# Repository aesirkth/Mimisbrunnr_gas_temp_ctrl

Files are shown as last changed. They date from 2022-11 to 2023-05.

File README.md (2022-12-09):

# Mimisbrunnr_gas_temp_ctrl

Mímisbrunnr gas tank temperature control unit

Project hierarchy: Mjölnir → Mimisbrunnr

## About

Mímisbrunnur is a temperature control unit that controls the temperature of the N<sub>2</sub> gas tank that is used as the oxidizer for the Mjölnir rocket.
The unit will regulate the temperature the desired temperature.
It will measure the temperature of the tank and then turn on a pump to allow warm water to flow in a tube around the tank.

## Requirements
1. Regulate the temperature of the oxidizer gas tank for the Mjölnir rocket
2. Manual as well as digital controls
    1. Manual control:
        1. Screen to see configurations
        2. Buttons to control
    2. Digital control:
        1. Connect through wifi and integrated into the system of Mjölnir
        2. Option to connect through CAN bus
3. Measure the temperature
    1. Have 3 temperature sensors: 1 top, 1 middle, 1 bottom
4. Turn a water pump to heat the tank
5. Tolerate rainy, snowy or other similar weather conditions

### Optional Requirements
1. Control heating element
2. Fully Waterproof

## Usage

Buttons to navigate

Connectors

## PCB

## Box

## Software

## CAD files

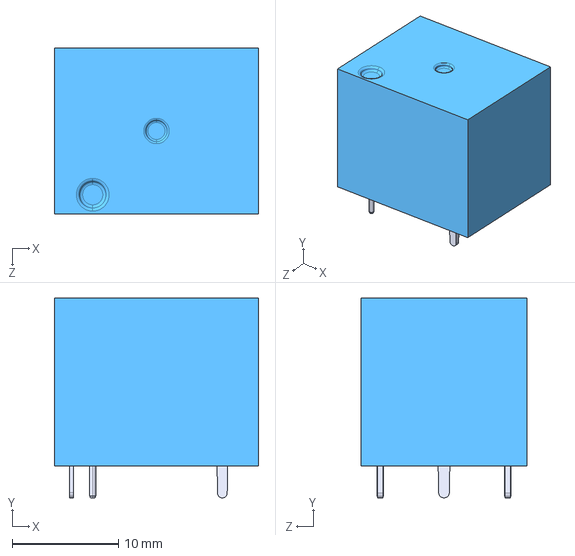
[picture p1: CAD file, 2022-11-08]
Mimisbrunnr_PCB/external components/SRD-12VDC-SL-C/SRD-12VDC-SL-C.step
19.2 x 18.8 x 15.6 mm

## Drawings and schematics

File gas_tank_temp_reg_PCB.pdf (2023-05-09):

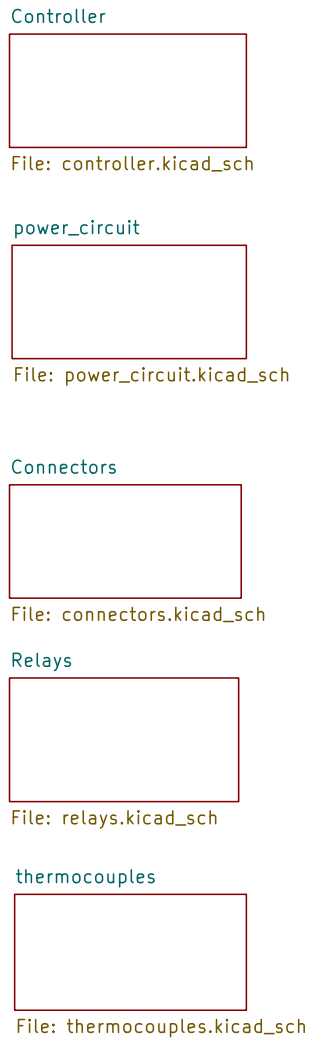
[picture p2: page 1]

Relays File: relays.kicad_sch Controller File: controller.kicad_sch Connectors File: connectors.kicad_sch

Id: 1/6 Title: File: gas_tank_temp_reg_PCB.kicad_sch Sheet: /

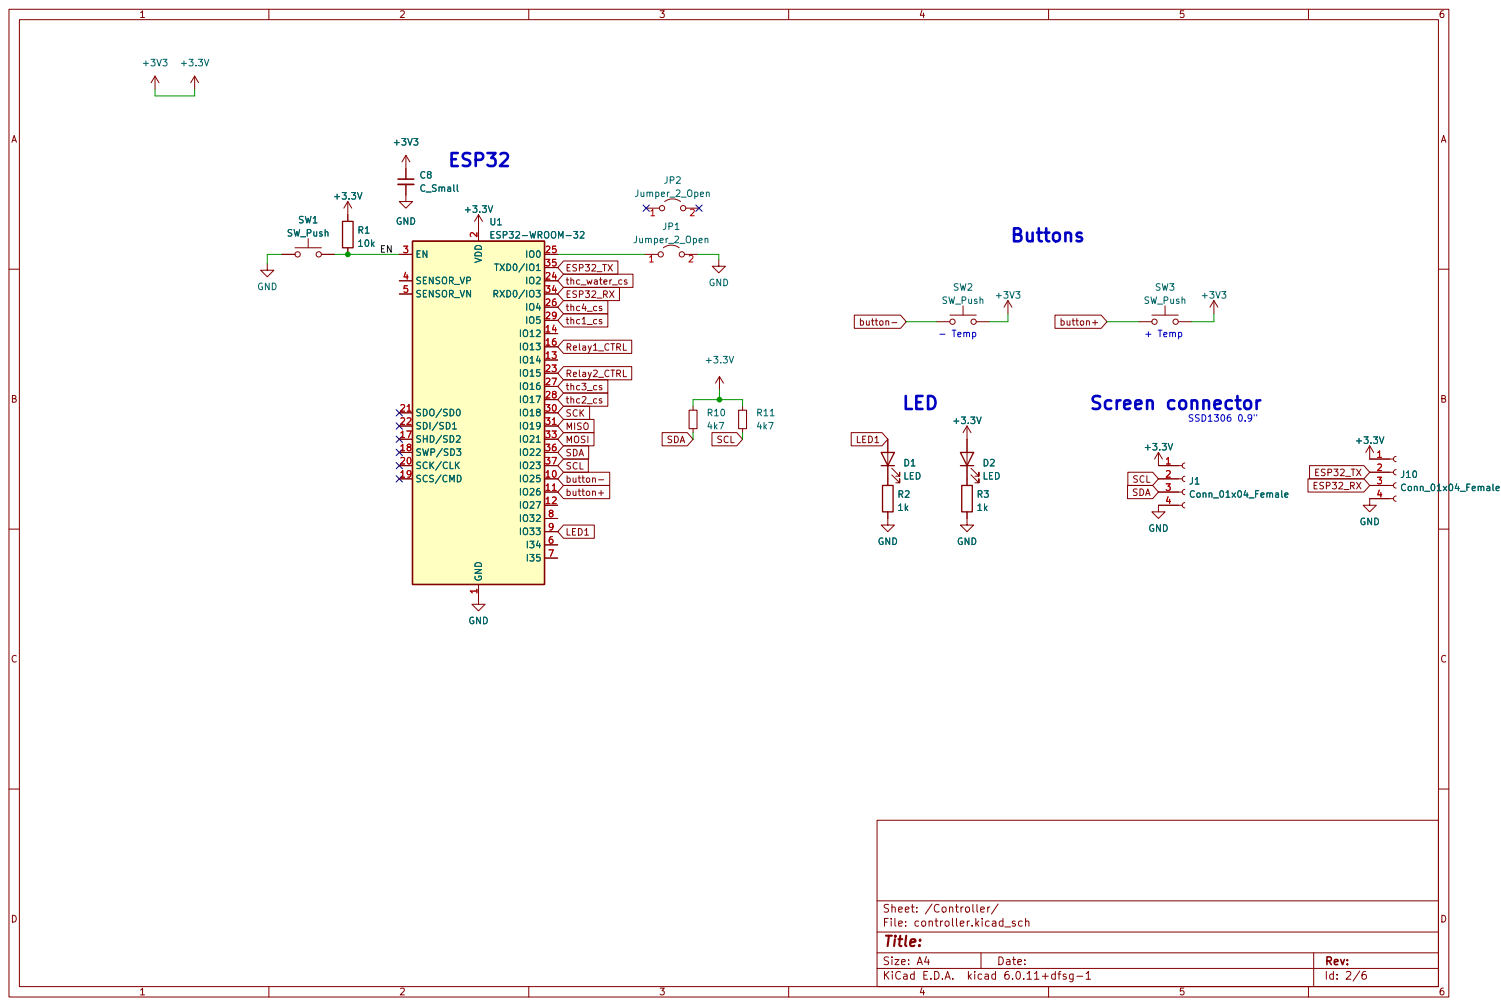
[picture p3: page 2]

2 SCK/CLK 20 SDO/SD0 21 SDI/SD1 22

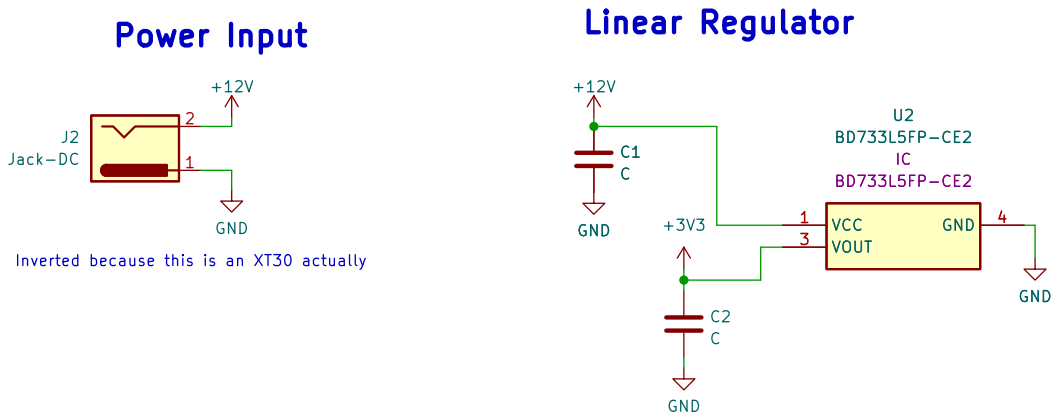
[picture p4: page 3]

Inverted because this is an XT30 actually

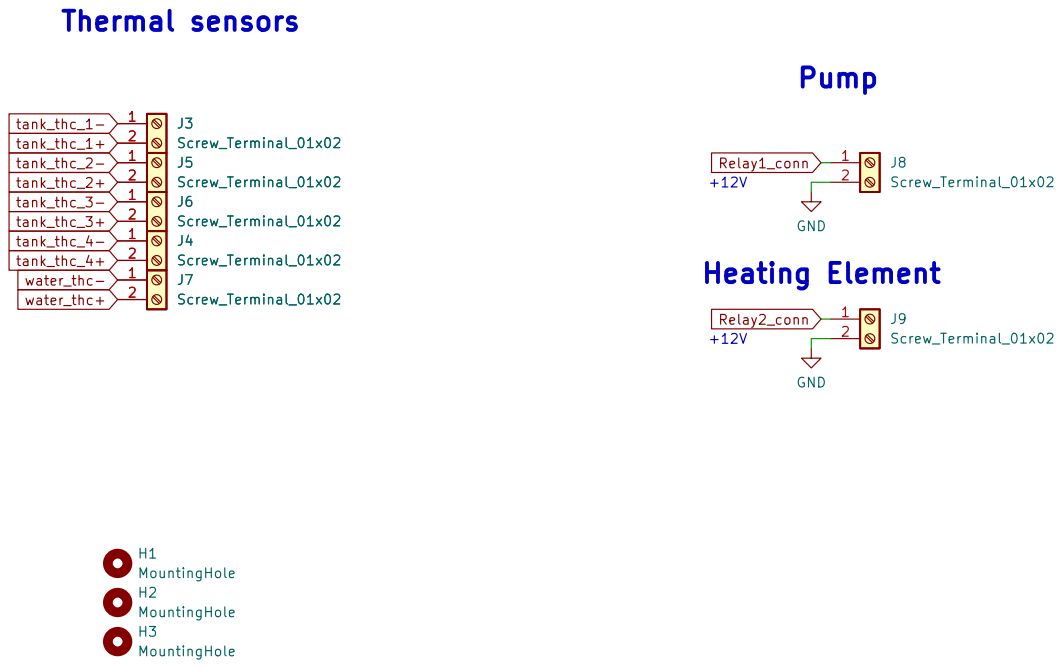
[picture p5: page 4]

Id: 4/6 Title: File: connectors.kicad_sch Sheet: /Connectors/ GND
+12V Heating Element

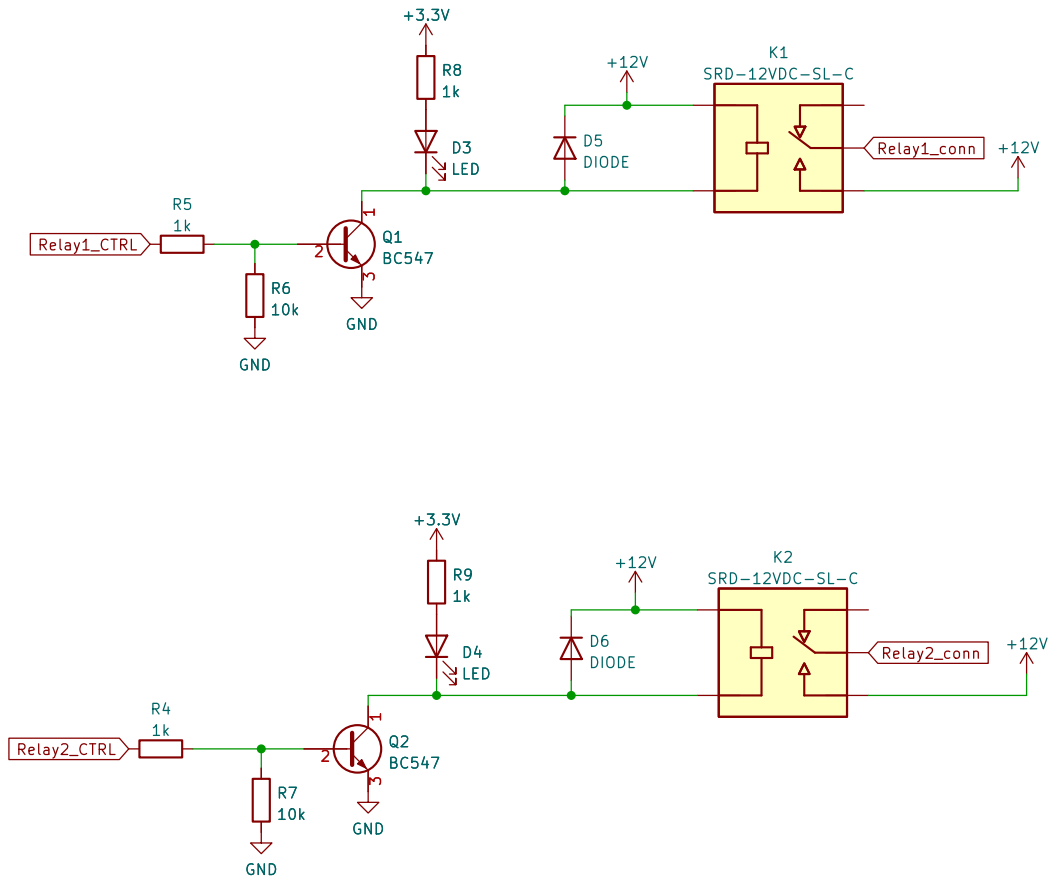
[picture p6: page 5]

Id: 5/6 Title: File: relays.kicad_sch Sheet: /Relays/

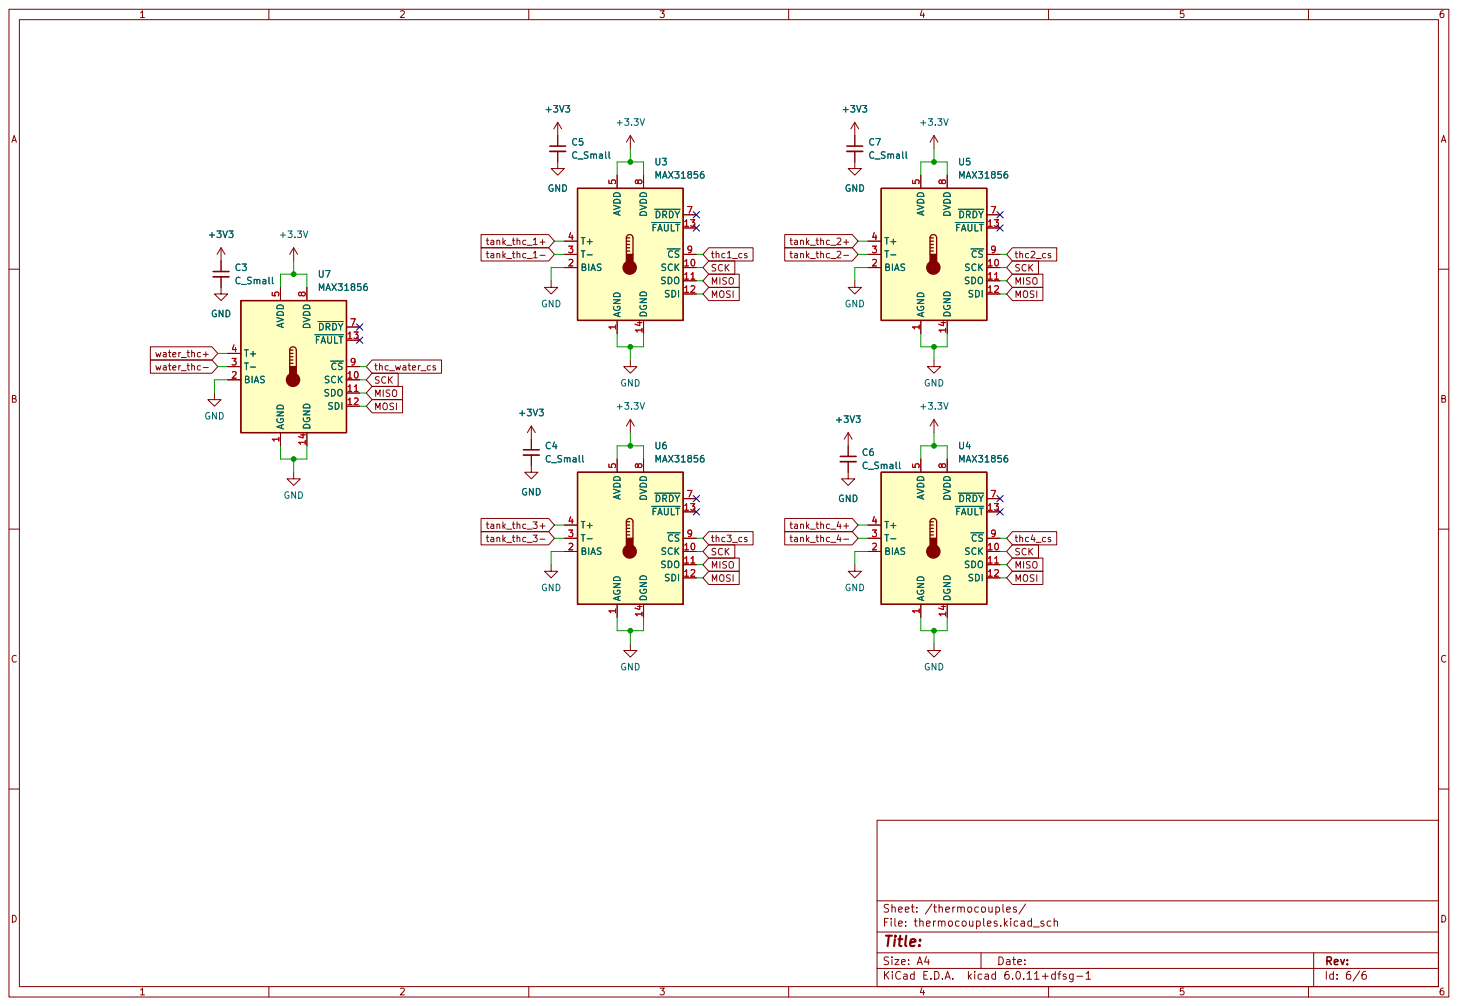
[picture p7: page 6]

1 SCK 10 SDO 11 SDI 12 ~{FAULT} 13 DGND 14 BIAS 2 T- 3 T+

8 ~{CS}9 U6 MAX31856 GND GND MISO

Id: 6/6 Title: File: thermocouples.kicad_sch Sheet: /thermocouples/

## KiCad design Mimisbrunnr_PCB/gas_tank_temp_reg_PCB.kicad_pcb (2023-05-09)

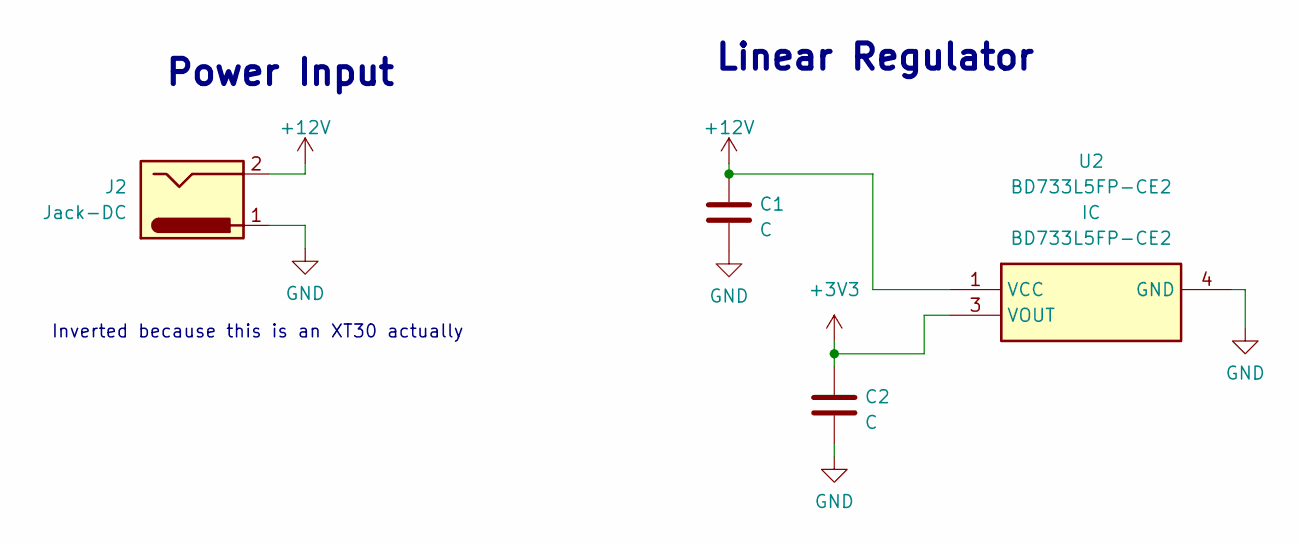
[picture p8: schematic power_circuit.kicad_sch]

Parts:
C1, C2: C; C_0805_2012Metric
J2: Jack-DC; AMASS_XT30PW-M_1x02_P2.50mm_Horizontal
U2: BD733L5FP-CE2; BD750L5FPCE2; Mouser Part Number 755-BD733L5FP-CE2

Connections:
+3.3V: C2.1, U2.3 (VOUT); also elsewhere on the board
+12V: C1.1, J2.2, U2.1 (VCC); also elsewhere on the board
GND: C1.2, C2.2, J2.1, U2.4 (GND); also elsewhere on the board

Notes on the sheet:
Power Input
Linear Regulator
Inverted because this is an XT30 actually

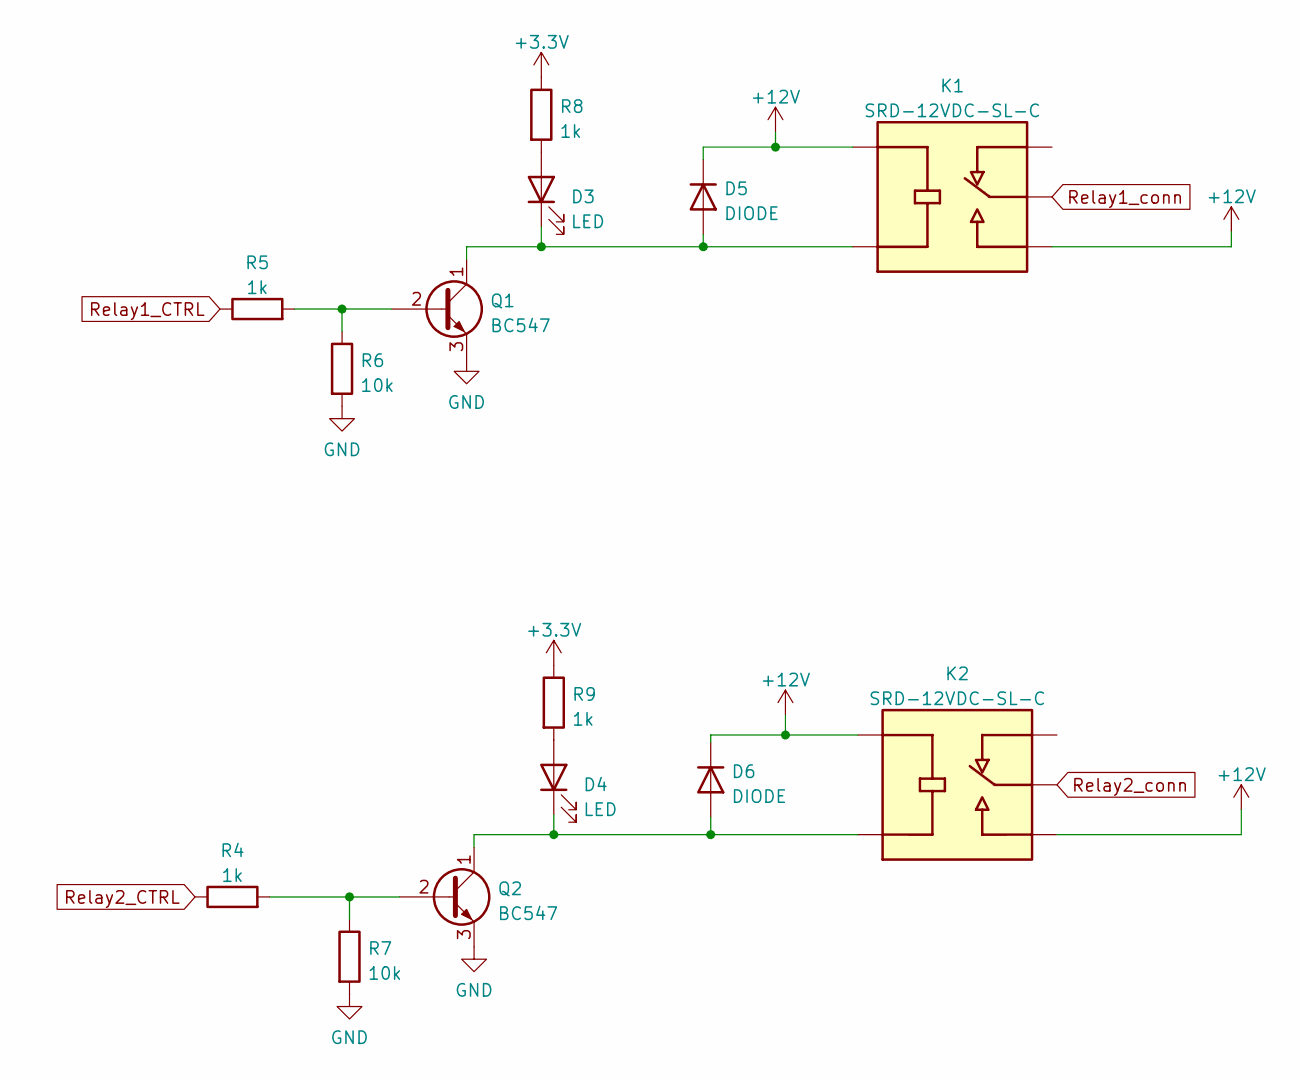
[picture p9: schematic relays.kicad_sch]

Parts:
D3, D4: LED; LED_0805_2012Metric
D5, D6: DIODE; D_0805_2012Metric
K1, K2: SRD-12VDC-SL-C; RELAY_SRD-12VDC-SL-C; PARTREV 1.0
Q1, Q2: BC547; TO-92_Inline
R4, R5, R8, R9: 1k; R_0805_2012Metric
R6, R7: 10k; R_0805_2012Metric

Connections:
+3.3V: R8.1, R9.1; also elsewhere on the board
+12V: D5.2 (K), D6.2 (K), K1.COIL1, K1.NO, K2.COIL1, K2.NO; also elsewhere on the board
GND: Q1.3 (E), Q2.3 (E), R6.2, R7.2; also elsewhere on the board
unnamed: D3.1 (K), D5.1 (A), K1.COIL2, Q1.1 (C)
unnamed: D3.2 (A), R8.2
unnamed: D4.1 (K), D6.1 (A), K2.COIL2, Q2.1 (C)
unnamed: D4.2 (A), R9.2
unnamed: Q1.2 (B), R5.2, R6.1
unnamed: Q2.2 (B), R4.2, R7.1
Relay1_CTRL: R5.1; also elsewhere on the board
Relay1_conn: K1.COM; also elsewhere on the board
Relay2_CTRL: R4.1; also elsewhere on the board
Relay2_conn: K2.COM; also elsewhere on the board

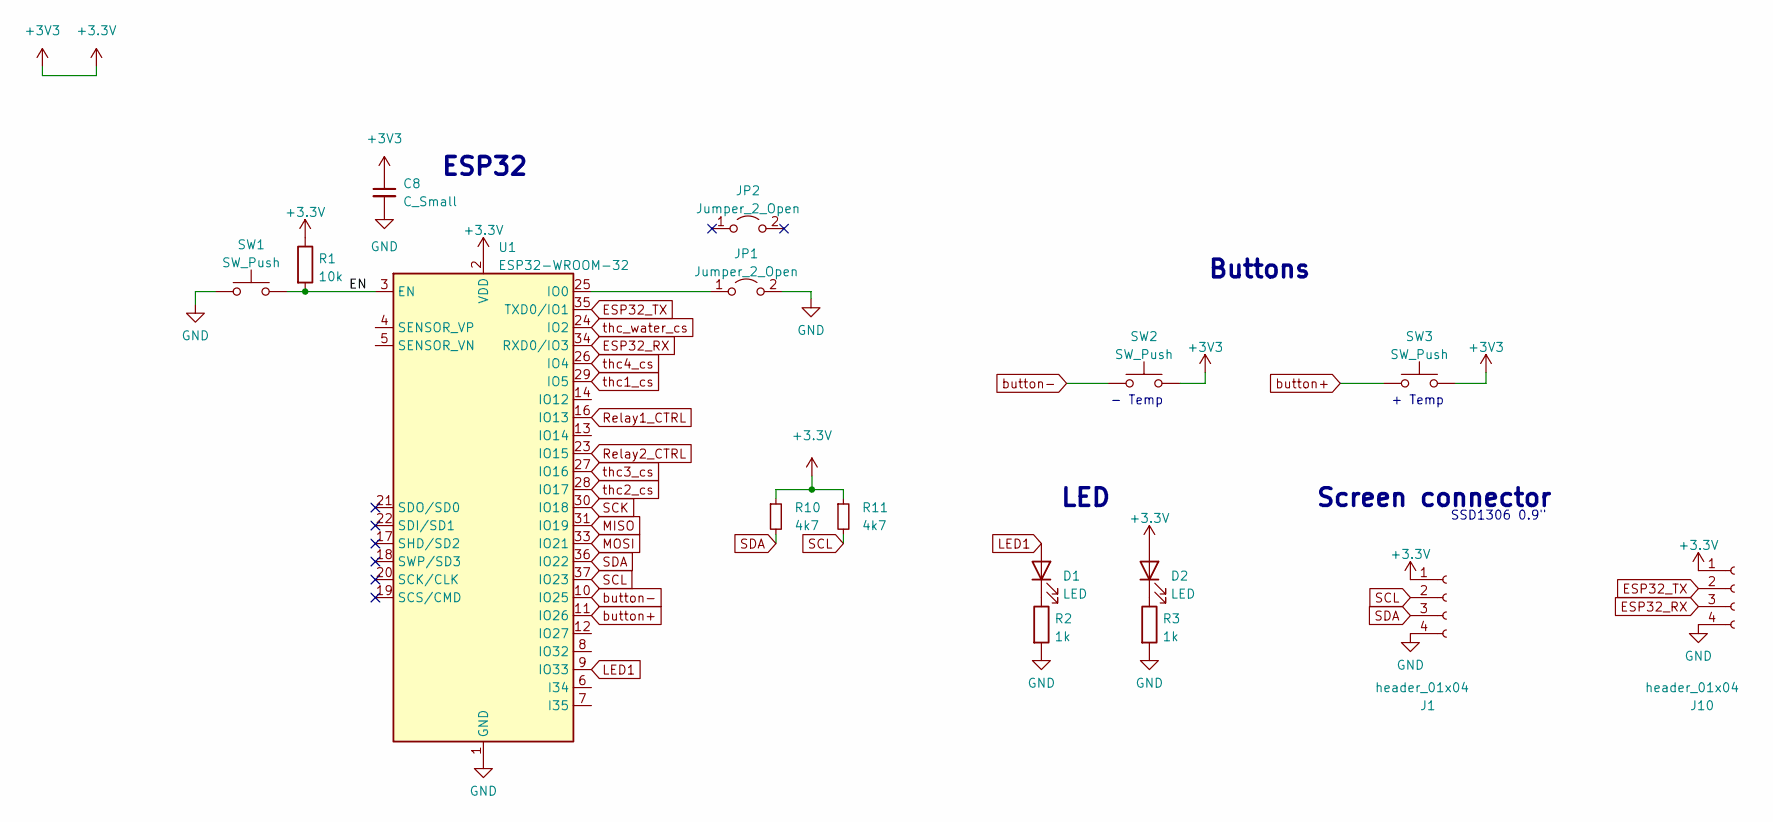
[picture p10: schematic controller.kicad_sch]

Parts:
C8: C_Small; C_0805_2012Metric
D1, D2: LED; LED_0805_2012Metric
J1, J10: header_01x04; PinHeader_1x04_P2.54mm_Vertical
JP1, JP2: Jumper_2_Open; PinHeader_1x02_P2.54mm_Vertical
R1: 10k; R_0805_2012Metric
R2, R3: 1k; R_0805_2012Metric
R10, R11: 4k7; R_0805_2012Metric
SW1, SW2, SW3: SW_Push; SW_SPST_B3U-1000P
U1: ESP32-WROOM-32

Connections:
+3.3V: C8.1, D2.2 (A), J1.1, J10.1, R1.1, R10.1, R11.1, SW2.2, SW3.2, U1.2 (VDD); also elsewhere on the board
/Controller/EN: R1.2, SW1.2, U1.3 (EN)
ESP32_RX: J10.3, U1.34 (RXD0/IO3)
ESP32_TX: J10.2, U1.35 (TXD0/IO1)
GND: C8.2, J1.4, J10.4, JP1.2 (B), R2.2, R3.2, SW1.1, U1.1 (GND), U1.15 (GND), U1.38 (GND), U1.39 (GND); also elsewhere on the board
LED1: D1.2 (A), U1.9 (IO33)
MISO: U1.31 (IO19); also elsewhere on the board
MOSI: U1.33 (IO21); also elsewhere on the board
unnamed: D1.1 (K), R2.1
unnamed: D2.1 (K), R3.1
unnamed: JP1.1 (A), U1.25 (IO0)
Relay1_CTRL: U1.16 (IO13); also elsewhere on the board
Relay2_CTRL: U1.23 (IO15); also elsewhere on the board
SCK: U1.30 (IO18); also elsewhere on the board
SCL: J1.2, R11.2, U1.37 (IO23)
SDA: J1.3, R10.2, U1.36 (IO22)
button+: SW3.1, U1.11 (IO26)
button-: SW2.1, U1.10 (IO25)
thc1_cs: U1.29 (IO5); also elsewhere on the board
thc2_cs: U1.28 (IO17); also elsewhere on the board
thc3_cs: U1.27 (IO16); also elsewhere on the board
thc4_cs: U1.26 (IO4); also elsewhere on the board
thc_water_cs: U1.24 (IO2); also elsewhere on the board

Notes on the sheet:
Buttons
Screen connector
+ Temp
ESP32
- Temp
LED
SSD1306 0.9"

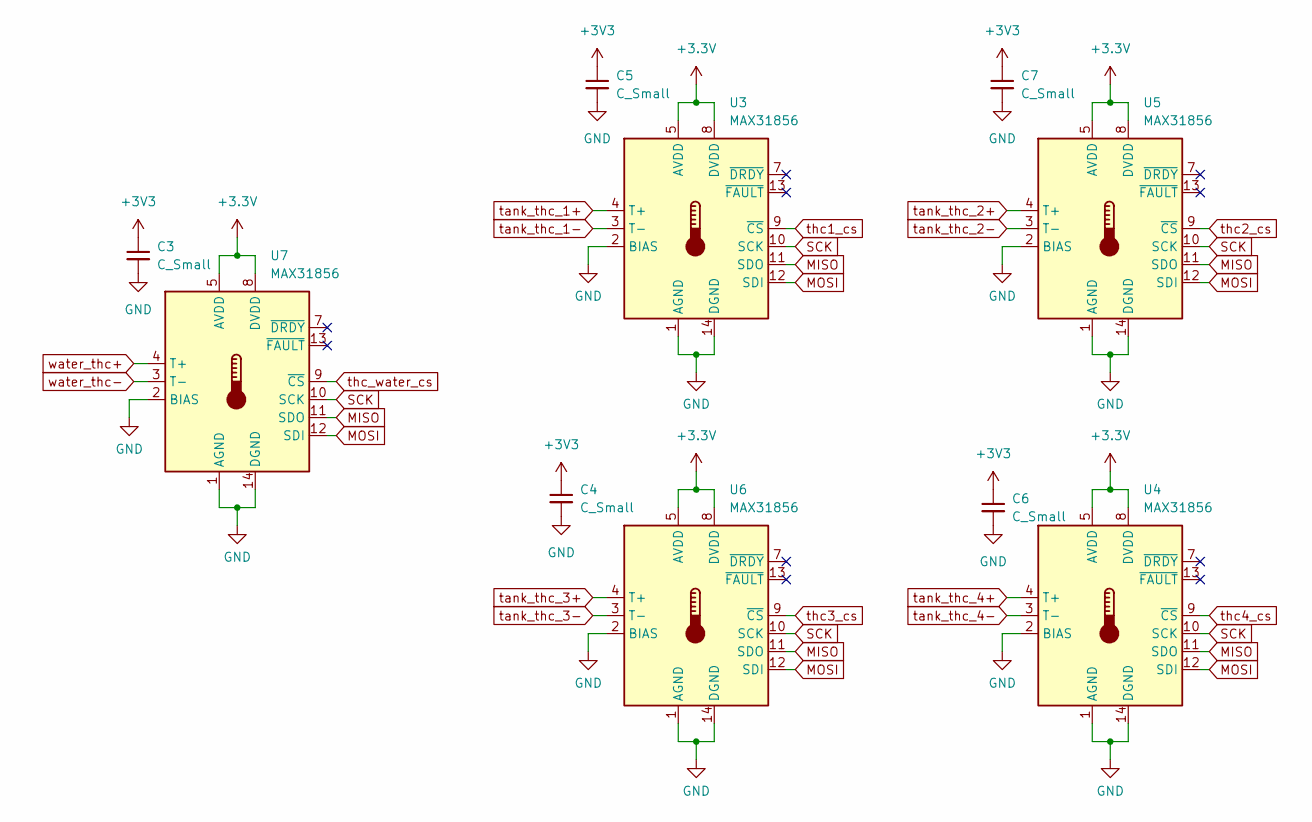
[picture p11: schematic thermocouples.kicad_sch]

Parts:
C3, C4, C5, C6, C7: C_Small; C_0805_2012Metric
U3, U4, U5, U6, U7: MAX31856; TSSOP-14_4.4x5mm_P0.65mm

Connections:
+3.3V: C3.1, C4.1, C5.1, C6.1, C7.1, U3.5 (AVDD), U3.8 (DVDD), U4.5 (AVDD), U4.8 (DVDD), U5.5 (AVDD), U5.8 (DVDD), U6.5 (AVDD), U6.8 (DVDD), U7.5 (AVDD), U7.8 (DVDD); also elsewhere on the board
GND: C3.2, C4.2, C5.2, C6.2, C7.2, U3.1 (AGND), U3.2 (BIAS), U3.14 (DGND), U4.1 (AGND), U4.2 (BIAS), U4.14 (DGND), U5.1 (AGND), U5.2 (BIAS), U5.14 (DGND), U6.1 (AGND), U6.2 (BIAS), U6.14 (DGND), U7.1 (AGND), U7.2 (BIAS), U7.14 (DGND); also elsewhere on the board
MISO: U3.11 (SDO), U4.11 (SDO), U5.11 (SDO), U6.11 (SDO), U7.11 (SDO); also elsewhere on the board
MOSI: U3.12 (SDI), U4.12 (SDI), U5.12 (SDI), U6.12 (SDI), U7.12 (SDI); also elsewhere on the board
SCK: U3.10 (SCK), U4.10 (SCK), U5.10 (SCK), U6.10 (SCK), U7.10 (SCK); also elsewhere on the board
tank_thc_1+: U3.4 (T+); also elsewhere on the board
tank_thc_1-: U3.3 (T-); also elsewhere on the board
tank_thc_2+: U5.4 (T+); also elsewhere on the board
tank_thc_2-: U5.3 (T-); also elsewhere on the board
tank_thc_3+: U6.4 (T+); also elsewhere on the board
tank_thc_3-: U6.3 (T-); also elsewhere on the board
tank_thc_4+: U4.4 (T+); also elsewhere on the board
tank_thc_4-: U4.3 (T-); also elsewhere on the board
thc1_cs: U3.9 (~CS); also elsewhere on the board
thc2_cs: U5.9 (~CS); also elsewhere on the board
thc3_cs: U6.9 (~CS); also elsewhere on the board
thc4_cs: U4.9 (~CS); also elsewhere on the board
thc_water_cs: U7.9 (~CS); also elsewhere on the board
water_thc+: U7.4 (T+); also elsewhere on the board
water_thc-: U7.3 (T-); also elsewhere on the board

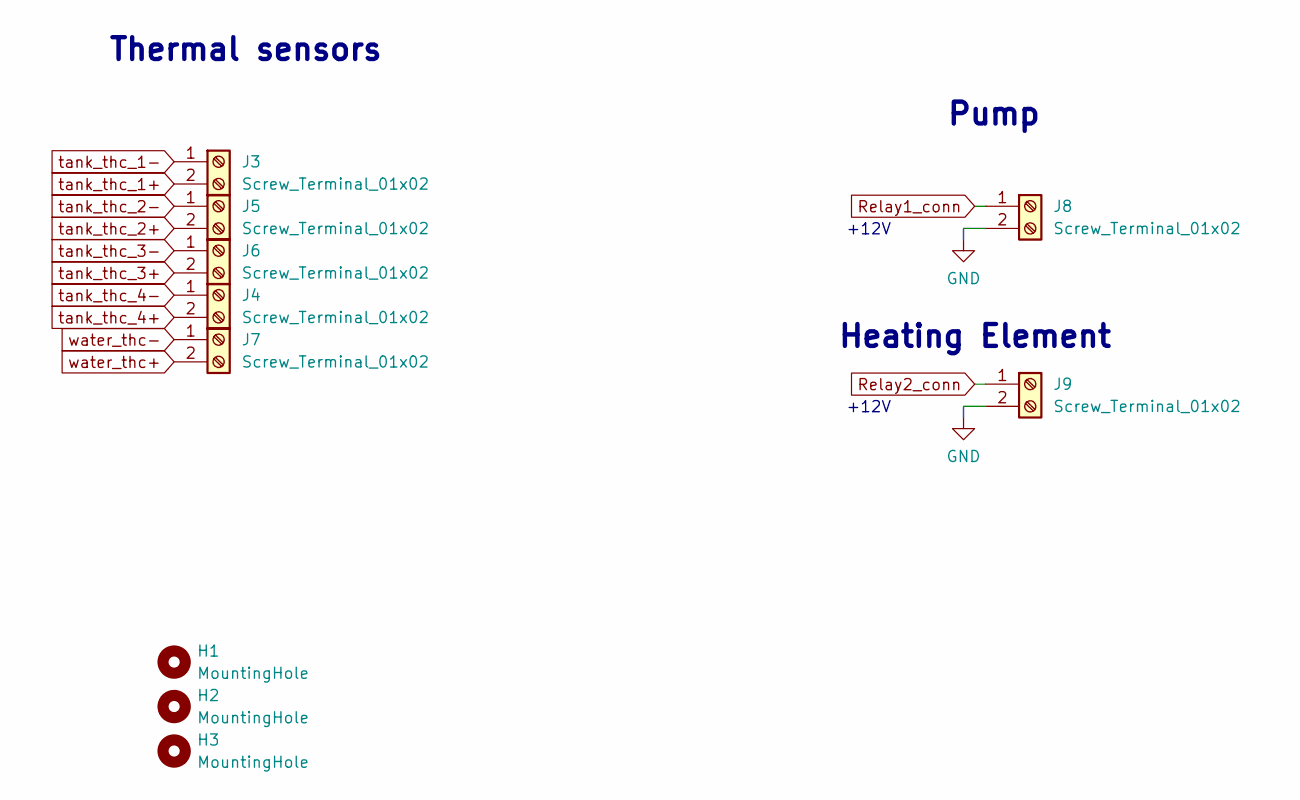
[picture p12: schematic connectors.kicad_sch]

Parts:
H1, H2, H3: MountingHole; MountingHole_3.2mm_M3
J3, J4, J5, J6, J7, J8, J9: Screw_Terminal_01x02; TerminalBlock_TE_282834-2_1x02_P2.54mm_Horizontal

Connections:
GND: J8.2, J9.2; also elsewhere on the board
Relay1_conn: J8.1; also elsewhere on the board
Relay2_conn: J9.1; also elsewhere on the board
tank_thc_1+: J3.2; also elsewhere on the board
tank_thc_1-: J3.1; also elsewhere on the board
tank_thc_2+: J5.2; also elsewhere on the board
tank_thc_2-: J5.1; also elsewhere on the board
tank_thc_3+: J6.2; also elsewhere on the board
tank_thc_3-: J6.1; also elsewhere on the board
tank_thc_4+: J4.2; also elsewhere on the board
tank_thc_4-: J4.1; also elsewhere on the board
water_thc+: J7.2; also elsewhere on the board
water_thc-: J7.1; also elsewhere on the board

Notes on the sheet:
Heating Element
+12V
Pump
Thermal sensors

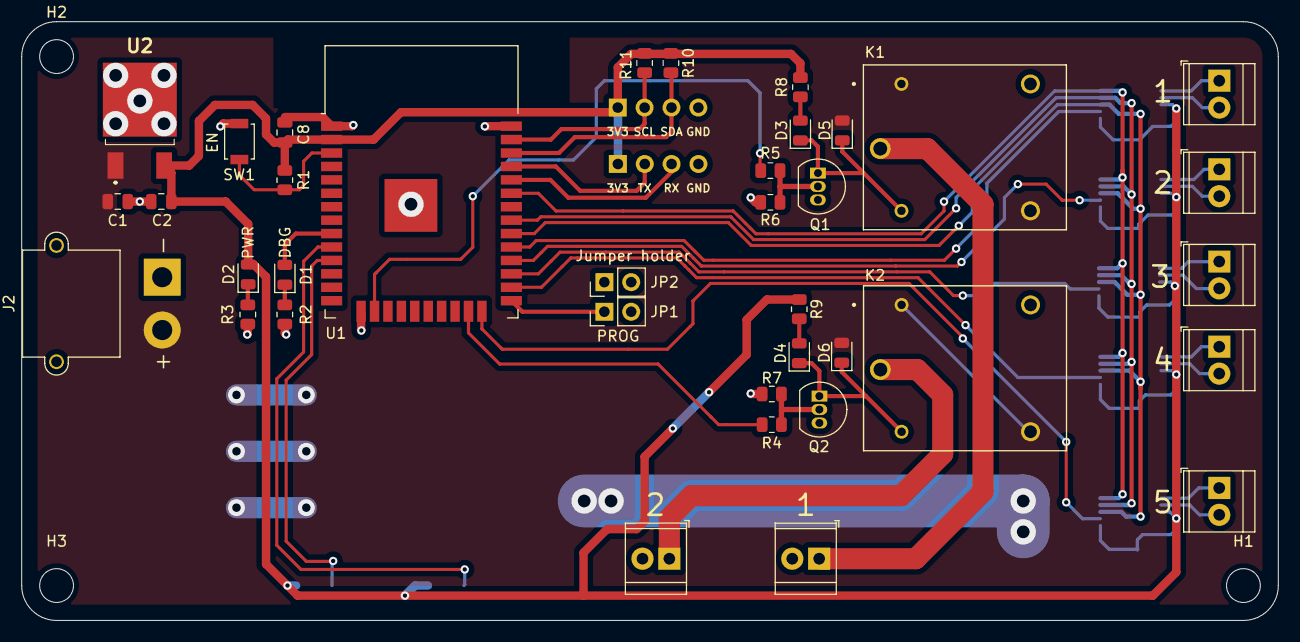
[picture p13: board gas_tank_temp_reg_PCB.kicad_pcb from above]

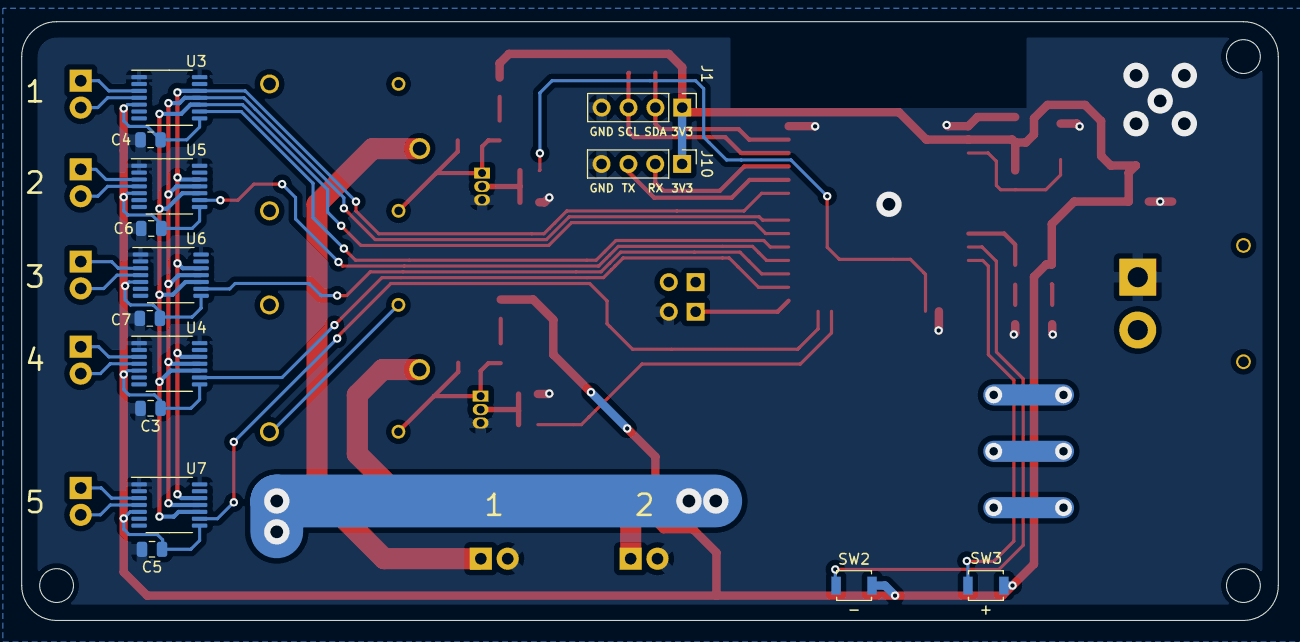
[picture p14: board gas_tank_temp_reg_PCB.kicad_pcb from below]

Board: 2 copper layers, 118.9 x 56.6 mm, 54 parts (14 on the bottom side), 42 nets.

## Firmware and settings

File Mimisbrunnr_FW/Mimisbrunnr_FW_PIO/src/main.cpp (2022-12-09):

#include <Arduino.h>

#include <Wire.h>
#include <Adafruit_GFX.h>
#include <Adafruit_SSD1306.h>

#include "screen_UI.h"

 
void setup() {
  Serial.begin(115200);

  screen_UI_init();

  display_loading_screen(800);

  statusBtnOk = true;
}
 
void loop() {

  // reading_buttons();

  display_config_menu();
}

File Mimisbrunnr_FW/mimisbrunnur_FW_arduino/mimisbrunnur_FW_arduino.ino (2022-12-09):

/*********
  Rui Santos
  Complete project details at https://randomnerdtutorials.com  
*********/

#include <Wire.h>
#include <Adafruit_GFX.h>
#include <Adafruit_SSD1306.h>

#include "loading_screen.h"

#define SCREEN_WIDTH 128
#define SCREEN_HEIGHT 64

Adafruit_SSD1306 display(SCREEN_WIDTH, SCREEN_HEIGHT, &Wire, -1);


 
void setup() {
  Serial.begin(115200);
 
  if(!display.begin(SSD1306_SWITCHCAPVCC, 0x3C)) {
    Serial.println(F("SSD1306 allocation failed"));
    for(;;);
  }
  delay(1000); // Pause for 1 seconds
 
  // Clear the buffer.
  display.clearDisplay();
  display_loading_screen(display, 800);
}
 
void loop() {
  
}

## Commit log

2022-11-08 Init commit / Adding PCB project
    [SRD-12VDC-SL-C.step, connectors.kicad_sch, controller.kicad_sch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]
2022-12-09 Adding firmware to project. Some groundwork for the FW has been done
2023-04-16 finalize schematic
    [connectors.kicad_sch, controller.kicad_sch, gas_tank_temp_reg_PCB.kicad_pcb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]
2023-05-09 routing finished
    [connectors.kicad_sch, controller.kicad_sch, gas_tank_temp_reg_PCB.kicad_pcb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]
2023-05-09 Improve style
    [connectors.kicad_sch, controller.kicad_sch, gas_tank_temp_reg_PCB.kicad_pcb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]
